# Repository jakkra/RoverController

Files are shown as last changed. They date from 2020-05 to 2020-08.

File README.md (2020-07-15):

# Rover Controller
Controller for driving [https://github.com/jakkra/Mars-Rover](https://github.com/jakkra/Mars-Rover).
Webpage for viewing telematics graphs on phone [https://github.com/jakkra/Rover-Mission-Control](https://github.com/jakkra/Rover-Mission-Control).

## How it works
Sets up an AP, the Rover will automatically connect if it's in range.
The Rover is controlled by sending joystick and switch state over either LoRa or a websocket. If the Rover isn't connected to the AP, then data will be sent over LoRa instead. There is a switch to override this behaviour and always send data over LoRa even if the Rover is connected to the AP.

When the Rover is connected to the local AP it will send telematics data over the websocket, or over LoRa if the Rover is outside of WiFi range. The data is then in turn passed on to a phone if one is connected. When the Rover is close by telematics will arrive about 10/s over WiFi, if outide of range then telematics are transported over LoRa. As LoRa modules cannot do true duplex data transfer we need to switch between sending and receiving, meaning telematics sent by the rover while we are sending joystick data will be lost. From experimentation LoRa telematics arrive about every 500ms. 

A phone can connect to the Controller AP to view the telematics from the Rover. Phone opens a websocket connection to the Controller and receives the telematic data the Rover sends. Telematics website can be found here: https://github.com/jakkra/Rover-Mission-Control.

## CAD model
Full Fusion 360 project is found in `CAD` folder. 

## Hardware
- [ESP32 + LoRa module](https://www.banggood.com/2Pcs-LILYGO-TTGO-LORA32-868Mhz-ESP32-LoRa-OLED-0_96-Inch-Blue-Display-bluetooth-WIFI-ESP-32-Development-Board-Module-With-Antenna-p-1507044.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)
- 2x [Joysticks](https://www.ebay.com/sch/i.html?_from=R40&_trksid=m570.l1313&_nkw=JH-D400X-R4-10K-4D&_sacat=0)
- 1x ADS1115 (ESP32 does not have enough ADCs for all the pots)
- A few on-off-on switches
- 2 potentiometers
- 2 colored LEDs

## Config
For pinmapping see: https://github.com/jakkra/RoverController/blob/master/main/controller_input.c#L46

## Images

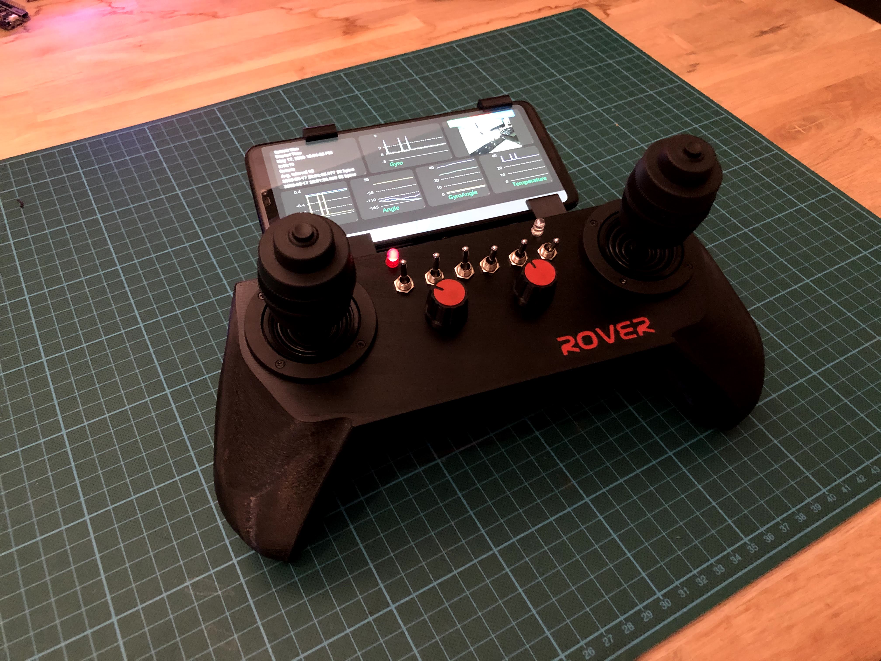
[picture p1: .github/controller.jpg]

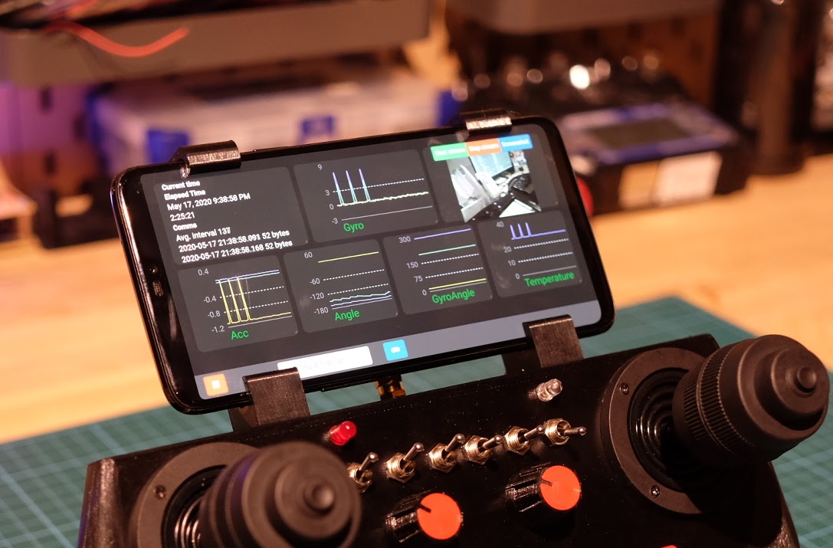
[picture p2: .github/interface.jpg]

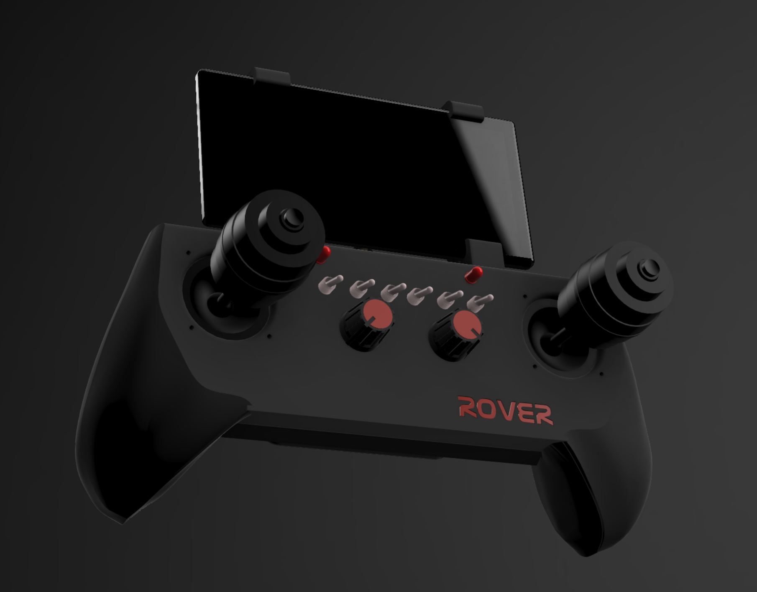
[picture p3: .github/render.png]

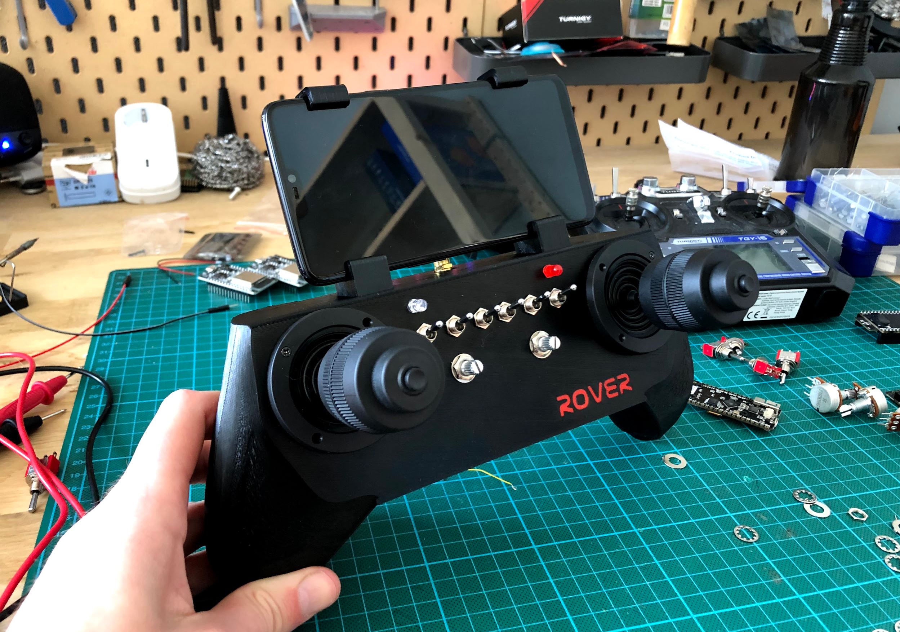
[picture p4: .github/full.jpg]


## Compiling
Follow instruction on [https://github.com/espressif/esp-idf](https://github.com/espressif/esp-idf) to set up the esp-idf, then just run `idf.py build` or use the [VSCode extension](https://github.com/espressif/vscode-esp-idf-extension).

## Building the controller
TBD upon request.

## esp-idf patches
Run `git apply esp-idf-patch/no_delay.patch` in your esp-idf folder. This decreases lag for TCP as it will flush the buffers after every write instead of LWIP buffering TCP data to send it in chunks.

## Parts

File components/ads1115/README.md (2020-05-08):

By Blake Felt - blake.w.felt@gmail.com

ESP32 ADS1115
=============

A component for TI ADS1115 on ESP-IDF. For an example, see https://github.com/Molorius/ESP32-Examples.

To add to a project, type:
`git submodule add https://github.com/Molorius/esp32-ads1115.git components/ads1115`
into the base directory of your project.

The datasheet can be found [here](http://www.ti.com/lit/ds/symlink/ads1115.pdf).

This has not been tested with more than one ADS1115 connected.
Any suggestions or fixes are gladly appreciated.

Table of Contents
=================

* [Enumerations](#enumerations)
  * [ads11115_mux_t](#enum-ads1115_mux_t)
  * [ads1115_fsr_t](#enum-ads1115_fsr_t)
  * [ads1115_sps_t](#enum-ads1115_sps_t)
  * [ads1115_mode_t](#enum-ads1115_mode_t)
* [Functions](#functions)
  * [ads1115_config](#ads1115_t-ads1115_configi2c_port_t-i2c_portuint8_t-address)
  * [ads1115_set_rdy_pin](#void-ads1115_set_rdy_pinads1115_t-adsgpio_num_t-gpio)
  * [ads1115_set_mux](#void-ads1115_set_muxads1115_t-adsads1115_mux_t-mux)
  * [ads1115_set_pga](#void-ads1115_set_pgaads1115_t-adsads1115_fsr_t-fsr)
  * [ads1115_set_mode](#void-ads1115_set_modeads1115_t-adsads1115_mode_t-mode)
  * [ads1115_set_sps](#void-ads1115_set_spsads1115_t-adsads1115_sps_t-sps)
  * [ads1115_set_max_ticks](#void-ads1115_set_max_ticksads1115_t-adsticktype_t-max_ticks)
  * [ads1115_get_raw](#int16_t-ads1115_get_rawads1115_t-ads)
  * [ads1115_get_voltage](#double-ads1115_get_voltageads1115_t-ads)

Enumerations
============

enum ads1115_mux_t
------------------

The different multiplexer options on the ADS1115.

*Values*
  * `ADS1115_MUX_0_1`: Connect pins 0 and 1.
  * `ADS1115_MUX_0_3`: Connect pins 0 and 3.
  * `ADS1115_MUX_1_3`: Connect pins 1 and 3.
  * `ADS1115_MUX_2_3`: Connect pins 2 and 3.
  * `ADS1115_MUX_0_GND`: Connect pin 0 to ground.
  * `ADS1115_MUX_1_GND`: Connect pin 1 to ground.
  * `ADS1115_MUX_2_GND`: Connect pin 2 to ground.
  * `ADS1115_MUX_3_GND`: Connect pin 3 to ground.

enum ads1115_fsr_t
------------------

The different full-scale resolution options.

*Values*
  * `ADS1115_FSR_6_144`: 6.144 volts
  * `ADS1115_FSR_4_096`: 4.096 volts
  * `ADS1115_FSR_2_048`: 2.048 volts
  * `ADS1115_FSR_1_024`: 1.024 volts
  * `ADS1115_FSR_0_512`: 0.512 volts
  * `ADS1115_FSR_0_256`: 0.256 volts

enum ads1115_sps_t
------------------

The different samples per second, or data rate, options.

*Values*
  * `ADS1115_SPS_8`: 8 samples per second
  * `ADS1115_SPS_16`: 16 samples per second
  * `ADS1115_SPS_32`: 32 samples per second
  * `ADS1115_SPS_64`: 64 samples per second
  * `ADS1115_SPS_128`: 128 samples per second
  * `ADS1115_SPS_250`: 250 samples per second
  * `ADS1115_SPS_475`: 475 samples per second
  * `ADS1115_SPS_860`: 860 samples per second

enum ads1115_mode_t
-------------------

Continuous or single-shot mode.

*Values*
  * `ADS1115_MODE_CONTINUOUS`: continuous mode.
  * `ADS1115_MODE_SINGLE`: single-shot mode.

Functions
=========

ads1115_t ads1115_config(i2c_port_t i2c_port,uint8_t address)
-------------------------------------------------------------

Setup of the device.

*Parameters*
  * `i2c_port`: the i2c bus number.
  * `address`: the device's i2c address.

*Returns*
  * The configuration file, which is passed to all subsequent functions.

*Notes*
  * This does not setup the i2c bus, this must be done before passing to this function.

void ads1115_set_rdy_pin(ads1115_t* ads,gpio_num_t gpio)
--------------------------------------------------------

Sets up an optional data-ready pin to verify when conversions are complete.
Connect to ALRT/RDY pin on ADS1115.

*Parameters*
  * `ads`: The configuration file.
  * `gpio`: The esp32 gpio. Do not setup beforehand.

void ads1115_set_mux(ads1115_t* ads,ads1115_mux_t mux)
------------------------------------------------------

Sets the pins to be multiplexed.

*Parameters*
  * `ads`: the configuration file.
  * `mux`: the desired multiplex option (see enumeration).

void ads1115_set_pga(ads1115_t* ads,ads1115_fsr_t fsr)
------------------------------------------------------

Sets the full-scale range, or the programmable-gain amplifier.

*Parameters*
  * `ads`: the configuration file.
  * `fsr`: the desired full-scale range option (see enumeration).

void ads1115_set_mode(ads1115_t* ads,ads1115_mode_t mode)
---------------------------------------------------------

Sets the read mode.

*Paremeters*
  * `ads`: the configuration file.
  * `mode`: the desired mode (see enumeration).

*Notes*
  * To end continuous mode, set it to single-shot mode and make one voltage read.

void ads1115_set_sps(ads1115_t* ads,ads1115_sps_t sps)
------------------------------------------------------

Sets the sampling speed.

*Parameters*
  * `ads`: the configuration file.
  * `sps`: the desired samples per second (see enumeration).

void ads1115_set_max_ticks(ads1115_t* ads,TickType_t max_ticks)
---------------------------------------------------------------

Sets the maximum wait ticks for the i2c reads and writes. See the [i2c documentation](http://esp-idf.readthedocs.io/en/latest/api-reference/peripherals/i2c.html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).

*Parameters*
  * `ads`: the configuration file.
  * `max_ticks`: maximum wait ticks.

int16_t ads1115_get_raw(ads1115_t* ads)
---------------------------------------

Reads the voltage based on the current configuration.

*Parameters*
  * `ads`: the configuration file.

*Returns*
  * The 16 bit raw voltage value directly from the ADS1115.

double ads1115_get_voltage(ads1115_t* ads)
------------------------------------------

Reads the voltage based on the current configuration.

*Parameters*
  * `ads`: the configuration file.

*Returns*
  * The voltage, based on the current full-scale range. This is just a conversion from the raw value.

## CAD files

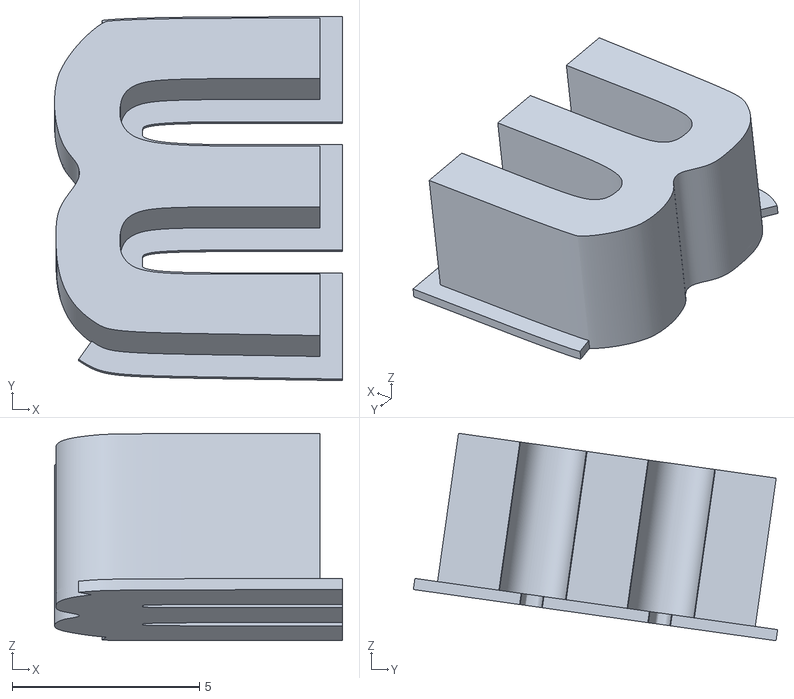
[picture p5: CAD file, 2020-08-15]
CAD/STL/text_e.stl
7.69 x 9.73 x 5.54

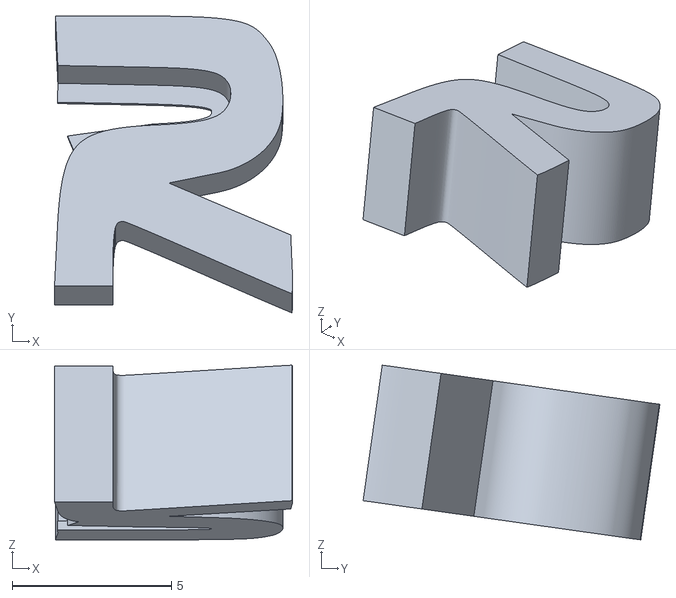
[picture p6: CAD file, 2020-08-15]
CAD/STL/text_r1.stl
7.48 x 9.32 x 5.49

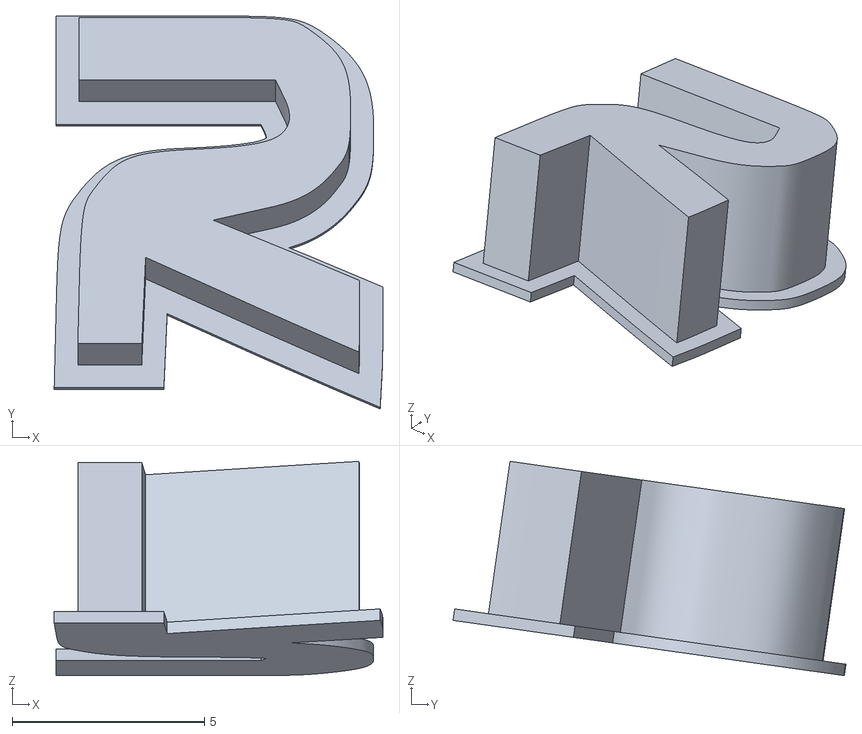
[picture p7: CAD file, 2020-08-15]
CAD/STL/text_r2.stl
8.54 x 10.2 x 5.57

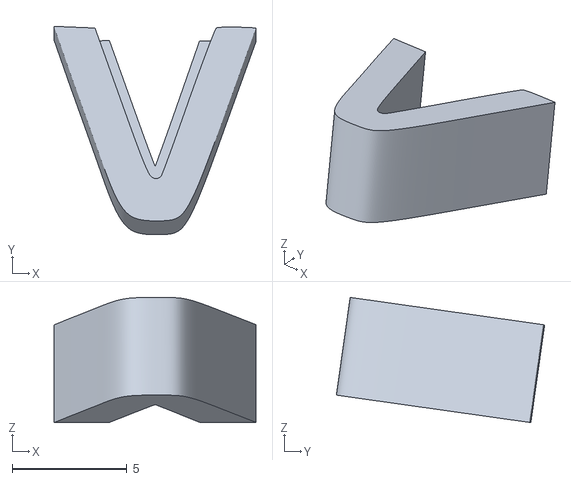
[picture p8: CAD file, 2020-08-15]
CAD/STL/text_v.stl
8.80 x 9.08 x 5.46

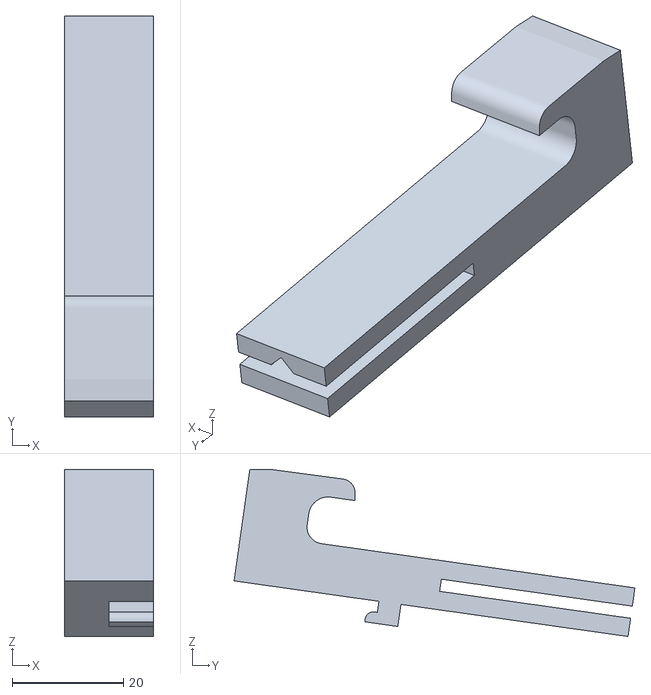
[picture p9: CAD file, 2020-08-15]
CAD/STL/holder_l_bottom.stl
16.0 x 71.9 x 30.0

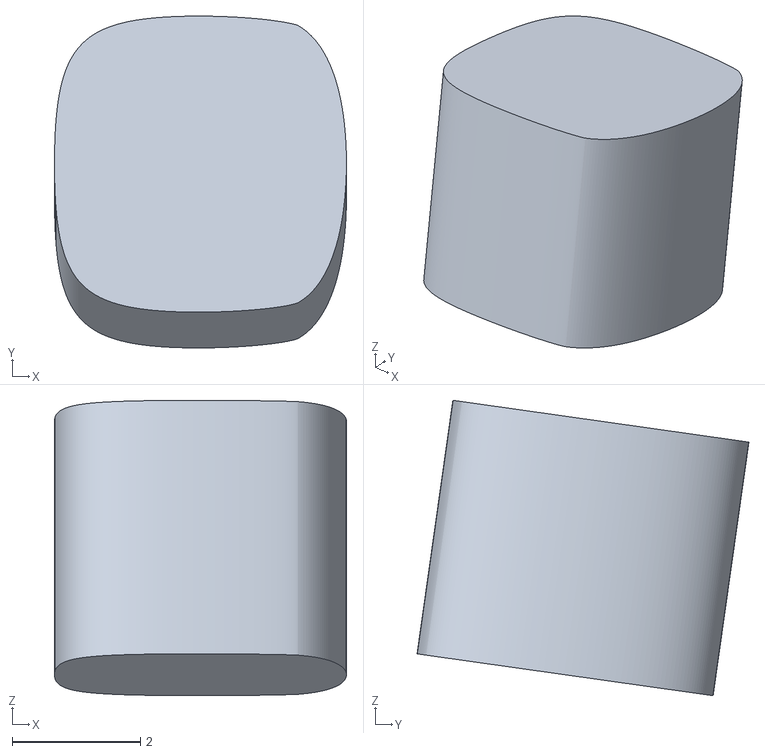
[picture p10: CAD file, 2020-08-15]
CAD/STL/text_inner_o.stl
4.56 x 5.19 x 4.61

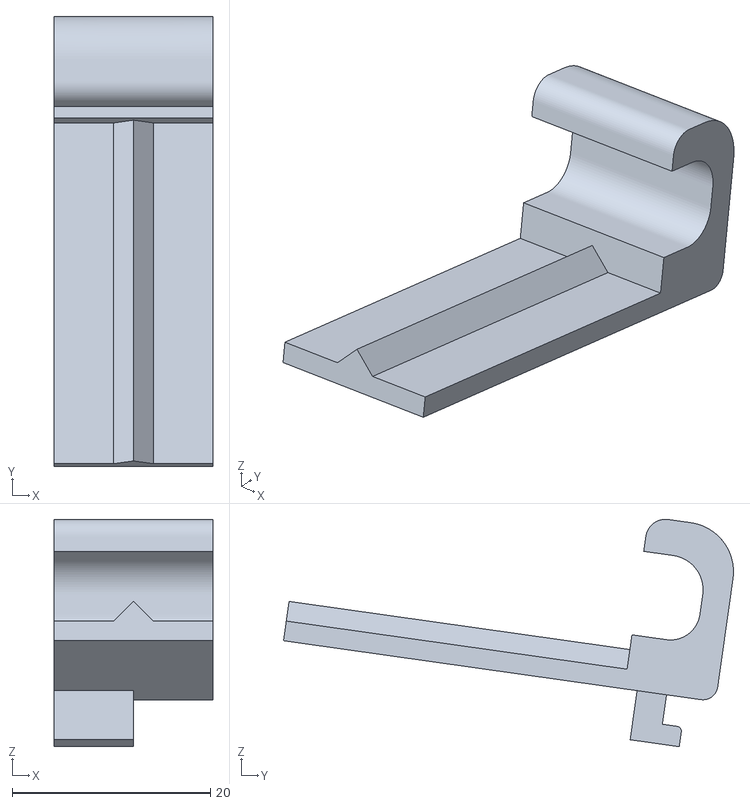
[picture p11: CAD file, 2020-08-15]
CAD/STL/holder_r_top.stl
16.0 x 45.4 x 22.9

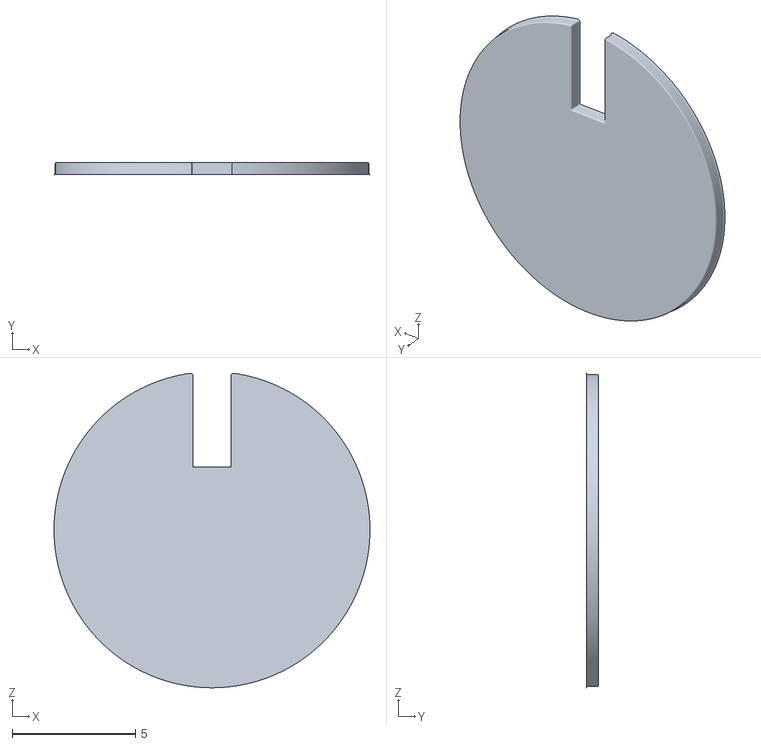
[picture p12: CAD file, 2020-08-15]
CAD/STL/knob_marker.stl
12.8 x 0.5 x 12.7

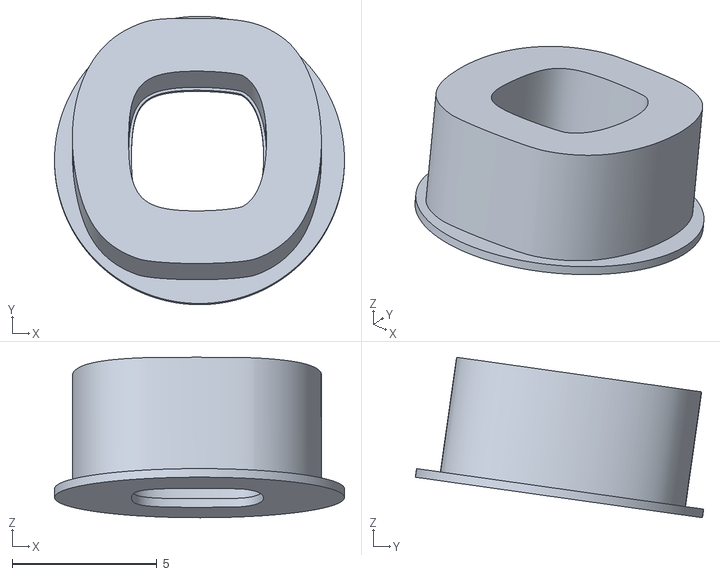
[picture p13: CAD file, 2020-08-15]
CAD/STL/text_o.stl
10.0 x 9.96 x 5.54

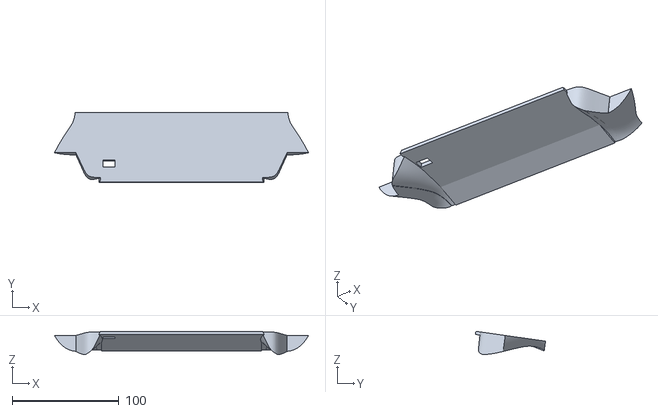
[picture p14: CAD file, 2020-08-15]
CAD/STL/back.stl
238.5 x 65.9 x 21.9

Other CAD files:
CAD/STL/holder_r_bottom.stl
CAD/STL/holder_l_top.stl

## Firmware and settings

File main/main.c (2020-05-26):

#include <stdio.h>
#include "string.h"
#include "freertos/FreeRTOS.h"
#include "freertos/task.h"
#include "esp_system.h"
#include "freertos/FreeRTOS.h"
#include "freertos/task.h"
#include "esp_system.h"
#include "esp_wifi.h"
#include "esp_event.h"
#include "esp_log.h"
#include "nvs_flash.h"
#include "transport_wifi.h"
#include "controller_input.h"
#include "rover_controller.h"
#include "leds.h"

#include "lwip/err.h"
#include "lwip/sys.h"

#include "web_server.h"
#include "config.h"
#include "transport_lora.h"

static const char *TAG = "main";

static void wifi_event_handler(void* arg, esp_event_base_t event_base, int32_t event_id, void* event_data)
{
    
    switch (event_id) {
        case WIFI_EVENT_AP_START:
            webserver_start();
            break;
        case WIFI_EVENT_AP_STOP:
            webserver_stop();
            break;
        case WIFI_EVENT_AP_STACONNECTED:
        {
            wifi_event_ap_staconnected_t* event = (wifi_event_ap_staconnected_t*) event_data;
            ESP_LOGW(TAG, "station "MACSTR" join, AID=%d", MAC2STR(event->mac), event->aid);
            break;
        }
        case WIFI_EVENT_AP_STADISCONNECTED:
        {
            wifi_event_ap_stadisconnected_t* event = (wifi_event_ap_stadisconnected_t*) event_data;
            ESP_LOGW(TAG, "station "MACSTR" leave, AID=%d", MAC2STR(event->mac), event->aid);
            break;
        }
    }
}

static void start_ap(void) {
    esp_netif_t* netif = esp_netif_create_default_wifi_ap();
    ESP_ERROR_CHECK(esp_netif_dhcps_stop(netif));
    esp_netif_ip_info_t ip_info;

    ip_info.ip.addr = esp_ip4addr_aton(ROVER_CONTROLLER_STATIC_IP);;
   	IP4_ADDR(&ip_info.gw, 192, 168, 1, 1);
   	IP4_ADDR(&ip_info.netmask, 255, 255, 255, 0);
    ESP_ERROR_CHECK(esp_netif_set_ip_info(netif, &ip_info));

    wifi_init_config_t cfg = WIFI_INIT_CONFIG_DEFAULT();
    ESP_ERROR_CHECK(esp_wifi_init(&cfg));

    ESP_ERROR_CHECK(esp_event_handler_instance_register(WIFI_EVENT, ESP_EVENT_ANY_ID, &wifi_event_handler, NULL, NULL));

    wifi_config_t wifi_config = {
        .ap = {
            .ssid = AP_SSID,
            .ssid_len = strlen(AP_SSID),
            .password = AP_PASS,
            .max_connection = 3,
            .authmode = WIFI_AUTH_WPA2_PSK
        },
    };
    if (strlen(AP_PASS) == 0) {
        wifi_config.ap.authmode = WIFI_AUTH_OPEN;
    }

    ESP_ERROR_CHECK(esp_wifi_set_mode(WIFI_MODE_AP));
    ESP_ERROR_CHECK(esp_wifi_set_config(ESP_IF_WIFI_AP, &wifi_config));
    ESP_ERROR_CHECK(esp_wifi_start());

    ESP_LOGI(TAG, "wifi_init_softap finished. SSID:%s password:%s", AP_SSID, AP_PASS);
}

void app_main(void)
{
    ESP_ERROR_CHECK(nvs_flash_init());
    ESP_ERROR_CHECK(esp_netif_init());
    ESP_ERROR_CHECK(esp_event_loop_create_default());

    leds_init();
    transport_lora_init();
    webserver_init();
    transport_ws_init();
    rover_controller_init();
    transport_ws_start();
    
    start_ap();
}

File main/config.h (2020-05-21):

#define WS_SERVER_PORT  80

#define AP_SSID                             "RoverController"
#define AP_PASS                             ""

#define ROVER_WS_URL                        "ws://192.168.4.5:80/ws"

// TODO could use mdns instead of hardcoding
#define ROVER_CONTROLLER_STATIC_IP          "192.168.4.1"
#define ROVER_STATIC_IP                     "192.168.4.5"
#define ROVER_CAM_STATIC_IP                 "192.168.4.6"

#define ROVER_CONTROLLER_MIN_TX_VALUE       1000
#define ROVER_CONTROLLER_MAX_TX_VALUE       2000

#define ROVER_CONTROLLER_SDA                GPIO_NUM_22
#define ROVER_CONTROLLER_SCL                GPIO_NUM_23

#define LED_RIGHT_GPIO                      GPIO_NUM_15
#define LED_LEFT_GPIO                       GPIO_NUM_12

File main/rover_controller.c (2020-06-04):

#include <string.h>
#include "freertos/FreeRTOS.h"
#include "freertos/task.h"
#include "freertos/semphr.h"
#include "esp_log.h"

#include "rover_controller.h"
#include "controller_input.h"
#include "transport_wifi.h"
#include "transport_lora.h"
#include "rover_utils.h"
#include "config.h"

#define ADC_SAMPLE_DELAY        100
#define MAX_TX_BUF_LEN          100

#define ADC_DATA_NOTIFICATION   1

static void sample_readings_done_callback(controller_sample_t* samples, uint8_t num_samples);
static void periodic_send_data(void* params);
static bool build_rover_payload(void);
static uint16_t convert_3_way_switch(uint32_t raw1, uint32_t raw2);
static bool should_use_wifi_transport(void);


static const char* TAG = "ROVER_CONTROLLER";

static TaskHandle_t task_handle;
static xSemaphoreHandle sem_handle;
static controller_sample_t controller_samples[INPUTS_END];

static uint16_t tx_buf[MAX_TX_BUF_LEN];
static uint16_t tx_buf_payload_len;

void rover_controller_init(void)
{
    sem_handle = xSemaphoreCreateBinary();
    assert(sem_handle != NULL);
    xSemaphoreGive(sem_handle);
    BaseType_t status = xTaskCreate(periodic_send_data, "send_values", 4096, NULL, tskIDLE_PRIORITY, &task_handle);
    assert(status == pdPASS);

    controller_input_init(ADC_SAMPLE_DELAY, &sample_readings_done_callback);
}

static void periodic_send_data(void* params)
{
    while (true) {
        uint32_t notification;
        assert(xTaskNotifyWait(ADC_DATA_NOTIFICATION, 0, &notification, portMAX_DELAY));
        assert(notification == ADC_DATA_NOTIFICATION);
        assert(xSemaphoreTake(sem_handle, portMAX_DELAY) == pdPASS);

        for (uint8_t i = 0; i < INPUTS_END; i++) {
            //printf("%d: Raw: %d  ", i, controller_samples[i].raw_value);
        }
        //printf("\n");
        bool payload_changed = build_rover_payload();
        xSemaphoreGive(sem_handle);
        if (true) {
            if (should_use_wifi_transport()) {
                transport_ws_send((uint8_t*)tx_buf, tx_buf_payload_len);
            } else {
                transport_lora_send((uint8_t*)tx_buf, tx_buf_payload_len);
            }
        }
    }
}

static bool build_rover_payload(void)
{
    bool payload_changed = true;
    uint16_t temp_tx_buf[MAX_TX_BUF_LEN];

    tx_buf_payload_len = 6 * sizeof(uint16_t); // Rover RC controller have 6 channels, limit to that for now for compatability

    temp_tx_buf[0] = 2000 + 1000 - map(controller_samples[INPUT_RIGHT_JOYSTICK_X].voltage, 0, 3300, 1000, 2000); // Steer joystick is inverted
    temp_tx_buf[1] = map(controller_samples[INPUT_RIGHT_JOYSTICK_Y].voltage, 0, 3300, 1000, 2000);
    temp_tx_buf[2] = map(controller_samples[INPUT_LEFT_JOYSTICK_X].voltage, 0, 3300, 1000, 2000);
    temp_tx_buf[3] = map(controller_samples[INPUT_LEFT_JOYSTICK_Y].voltage, 0, 3300, 1000, 2000);
    temp_tx_buf[4] = convert_3_way_switch(controller_samples[INPUT_SWITCH_1_UP].raw_value, controller_samples[INPUT_SWITCH_1_DOWN].raw_value);
    temp_tx_buf[5] = 1500;


    //TODO("Could do more here, like only send if something changed more than x")
    if (memcmp(temp_tx_buf, tx_buf, tx_buf_payload_len) == 0) {
        payload_changed = false;
    } else {
        memcpy(tx_buf, temp_tx_buf, tx_buf_payload_len);
    }
    //ESP_LOGW(TAG, "Send: %d, %d \t %d, %d \t %d, %d", tx_buf[0], tx_buf[1], tx_buf[2],  tx_buf[3], tx_buf[4], tx_buf[5]);
    return payload_changed;
}

static void sample_readings_done_callback(controller_sample_t* samples, uint8_t num_samples)
{
    assert(num_samples == INPUTS_END);
    if (xSemaphoreTake(sem_handle, pdMS_TO_TICKS(5)) == pdPASS) {
        memcpy(controller_samples, samples, sizeof(controller_sample_t) * num_samples);
        xSemaphoreGive(sem_handle);
    } else {
        ESP_LOGE(TAG, "Failed getting adc sample copy semaphore");
    }
    
    assert(xTaskNotify(task_handle, ADC_DATA_NOTIFICATION, eSetValueWithOverwrite) == pdPASS);
}

static uint16_t convert_3_way_switch(uint32_t up, uint32_t down)
{
    uint16_t value;

    if (up == 0 && down == 0) {
        value = 1500;
    } else if (up == 1) {
        value = 1000;
    } else {
        value = 2000;
    }

    return value;
} 

static bool should_use_wifi_transport(void)
{
    return convert_3_way_switch(controller_samples[INPUT_SWITCH_2_UP].raw_value, controller_samples[INPUT_SWITCH_2_DOWN].raw_value) == 2000;
}

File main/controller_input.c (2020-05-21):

#include <string.h>
#include "controller_input.h"
#include "config.h"
#include "freertos/FreeRTOS.h"
#include "freertos/task.h"
#include "driver/gpio.h"
#include "driver/i2c.h"
#include "driver/adc.h"
#include "esp_adc_cal.h"
#include "soc/adc_channel.h"
#include "rover_utils.h"
#include "esp_log.h"
#include "ads1115.h"

#define DEFAULT_VREF    1100
#define NO_OF_SAMPLES   32

#define ATTENUATION     ADC_ATTEN_DB_11
#define ADC_WIDTH       ADC_WIDTH_BIT_10

#define I2C_NUM         I2C_NUM_0

#define LAST_SWITCH     INPUT_SWITCH_3_UP


static uint16_t rover_channel_map[INPUTS_END] = {
    INPUT_LEFT_JOYSTICK_X,
    INPUT_LEFT_JOYSTICK_Y,
    INPUT_LEFT_JOYSTICK_ROTATE,
    INPUT_RIGHT_JOYSTICK_X,
    INPUT_RIGHT_JOYSTICK_Y,
    INPUT_RIGHT_JOYSTICK_ROTATE,
    INPUT_POT_LEFT,
    INPUT_POT_RIGHT,
    INPUT_SWITCH_1_UP,
    INPUT_SWITCH_1_DOWN,
    INPUT_SWITCH_2_UP,
    INPUT_SWITCH_2_DOWN,
    INPUT_SWITCH_3_UP,
    INPUT_SWITCH_3_DOWN,
    INPUT_SWITCH_4_UP,
    INPUT_SWITCH_4_DOWN,
    INPUT_SWITCH_5_UP,
    INPUT_SWITCH_5_DOWN,
};

// Mapping of all inputs to GPIO/ADC num
static uint16_t rover_pin_map[INPUTS_END] = {
    [INPUT_LEFT_JOYSTICK_X] = ADC1_GPIO39_CHANNEL,
    [INPUT_LEFT_JOYSTICK_Y] = ADC1_GPIO36_CHANNEL,
    [INPUT_LEFT_JOYSTICK_ROTATE] = ADC1_GPIO33_CHANNEL,
    [INPUT_RIGHT_JOYSTICK_X] = ADC1_GPIO34_CHANNEL,
    [INPUT_RIGHT_JOYSTICK_Y] = ADC1_GPIO35_CHANNEL,
    [INPUT_RIGHT_JOYSTICK_ROTATE] = ADC1_GPIO32_CHANNEL,
    [INPUT_POT_LEFT] = ADS1115_MUX_0_GND,
    [INPUT_POT_RIGHT] = ADS1115_MUX_1_GND,
    [INPUT_SWITCH_1_UP] = GPIO_NUM_25,
    [INPUT_SWITCH_1_DOWN] = GPIO_NUM_13,
    [INPUT_SWITCH_2_UP] = GPIO_NUM_17,
    [INPUT_SWITCH_2_DOWN] = GPIO_NUM_21,
    [INPUT_SWITCH_3_UP] = GPIO_NUM_22,
    [INPUT_SWITCH_3_DOWN] = GPIO_NUM_23,
    [INPUT_SWITCH_4_UP] = GPIO_NUM_15,
    [INPUT_SWITCH_4_DOWN] = GPIO_NUM_2,
    [INPUT_SWITCH_5_UP] = GPIO_NUM_4,
    [INPUT_SWITCH_5_DOWN] = GPIO_NUM_12, // Note: ESP32 won't start if pulled high at boot
};


static void print_char_val_type(esp_adc_cal_value_t val_type);
static void sample_task(void* params);

static controller_sample_t samples[INPUTS_END];
static esp_adc_cal_characteristics_t* adc_chars;
static uint16_t sleep_time;
static samples_callback* on_sample_done_callback;
static ads1115_t ads;

void controller_input_init(uint16_t time_between_samples_ms, samples_callback* callback)
{
    assert(callback != NULL);
    memset(samples, 0, sizeof(samples));

    on_sample_done_callback = callback;
    sleep_time = time_between_samples_ms;

    adc_chars = calloc(1, sizeof(esp_adc_cal_characteristics_t));
    esp_adc_cal_value_t val_type = esp_adc_cal_characterize(ADC_UNIT_1, ATTENUATION, ADC_WIDTH, DEFAULT_VREF, adc_chars);
    print_char_val_type(val_type);

    adc1_config_width(ADC_WIDTH);
    for (uint8_t i = 0; i < INPUT_ANALOG_END; i++) {
        adc1_config_channel_atten((adc1_channel_t)rover_pin_map[i], ATTENUATION);
    }

    for (uint8_t i = INPUT_ANALOG_I2C_END; i < LAST_SWITCH; i++) {
        gpio_pad_select_gpio((gpio_num_t)rover_pin_map[i]);
        gpio_set_direction((gpio_num_t)rover_pin_map[i], GPIO_MODE_INPUT);
        gpio_set_pull_mode((gpio_num_t)rover_pin_map[i], GPIO_PULLDOWN_ONLY);
    }

    ESP_ERROR_CHECK(i2c_driver_install(I2C_NUM, I2C_MODE_MASTER, 0, 0, 0));
    ESP_ERROR_CHECK(i2c_set_pin(I2C_NUM, ROVER_CONTROLLER_SDA, ROVER_CONTROLLER_SCL, true, true, I2C_MODE_MASTER));
    i2c_config_t conf = {
        .mode = I2C_MODE_MASTER,
        .sda_io_num = GPIO_NUM_22,
        .sda_pullup_en = GPIO_PULLUP_ENABLE,
        .scl_io_num = GPIO_NUM_23,
        .scl_pullup_en = GPIO_PULLUP_ENABLE,
        .master.clk_speed = 100000
    };
    ESP_ERROR_CHECK(i2c_param_config(I2C_NUM, &conf));

    ads = ads1115_config(I2C_NUM, 0x48);
    ads1115_set_sps(&ads, ADS1115_SPS_860);

    TaskHandle_t handle;
    BaseType_t status = xTaskCreate(sample_task, "gpio_sample_task", 4096, NULL, tskIDLE_PRIORITY, &handle);
    assert(status == pdPASS);
}

uint32_t controller_input_get_map(uint8_t id, uint32_t min, uint32_t max)
{
    assert(id < INPUT_ANALOG_END);
    uint32_t max_reading;
    switch (ADC_WIDTH) {
        case ADC_WIDTH_BIT_9:
            max_reading = 512;
            break;
        case ADC_WIDTH_BIT_10: 
            max_reading = 1024;
            break;
        case ADC_WIDTH_BIT_11:
            max_reading = 2048;
            break;
        case ADC_WIDTH_BIT_12:
            max_reading = 4096;
            break;
        default:
            assert(false);

    }

    return map(samples[id].raw_value, 0, max_reading, min, max);
}

static void sample_task(void* params)
{
    while (true) {
        for (uint8_t i = 0; i < INPUT_ANALOG_END; i++) {
            uint32_t adc_reading = 0;
            for (int sample = 0; sample < NO_OF_SAMPLES; sample++) {
                adc_reading += (uint32_t)adc1_get_raw((adc1_channel_t)rover_pin_map[i]);
            }
            adc_reading /= NO_OF_SAMPLES;
            samples[i].raw_value = adc_reading;
            samples[i].voltage = esp_adc_cal_raw_to_voltage(adc_reading, adc_chars);
        }

        for (uint8_t i = INPUT_ANALOG_END; i < INPUT_ANALOG_I2C_END; i++) {
            // Not used right now so skip
            //ads1115_set_mux(&ads, rover_pin_map[i]);
            //samples[i].raw_value = ads1115_get_raw(&ads);
            //samples[i].voltage = ads1115_get_voltage_from_raw(&ads, samples[i].raw_value) * 1000;
        }

        for (uint8_t i = INPUT_ANALOG_I2C_END; i < LAST_SWITCH; i++) {
            samples[i].raw_value = gpio_get_level((gpio_num_t)rover_pin_map[i]);
            samples[i].voltage = samples[i].raw_value == 0 ? 0 : 3300;
        }

        on_sample_done_callback(samples, INPUTS_END);
        vTaskDelay(pdMS_TO_TICKS(sleep_time));
    }
}

static void print_char_val_type(esp_adc_cal_value_t val_type)
{
    if (val_type == ESP_ADC_CAL_VAL_EFUSE_TP) {
        printf("Characterized using Two Point Value\n");
    } else if (val_type == ESP_ADC_CAL_VAL_EFUSE_VREF) {
        printf("Characterized using eFuse Vref\n");
    } else {
        printf("Characterized using Default Vref\n");
    }
}

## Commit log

2020-04-19 Base analog readings on voltage instead of raw value as the voltage value is characterized and therefore more accurate.
2020-04-19 Handle switches
2020-04-23 Add LoRa component driver
2020-04-25 Handle running on board without LoRa module.
2020-05-08 Add extra function to ads1115 to convert raw value to voltage.
2020-05-08 Got to many Joysticks and pots so ESP32 ADC pins are not enough, adds an external I2C ADC (ADS1115).
2020-05-17 Add LEDs to show connection state.
2020-05-17 Add CAD design (Fusion 360 project).
2020-05-21 GPIO pin changes
2020-06-04 Invert steering joystick
2020-08-15 Add STL files, fixes #1
    [back.stl, holder_l_bottom.stl, holder_l_top.stl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]
